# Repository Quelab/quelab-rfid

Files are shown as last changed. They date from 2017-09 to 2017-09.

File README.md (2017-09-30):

# Arduino Code for Quelab RFID reader
This project is intended to replace the code that was originally running on the RFID door control system for Quelab.

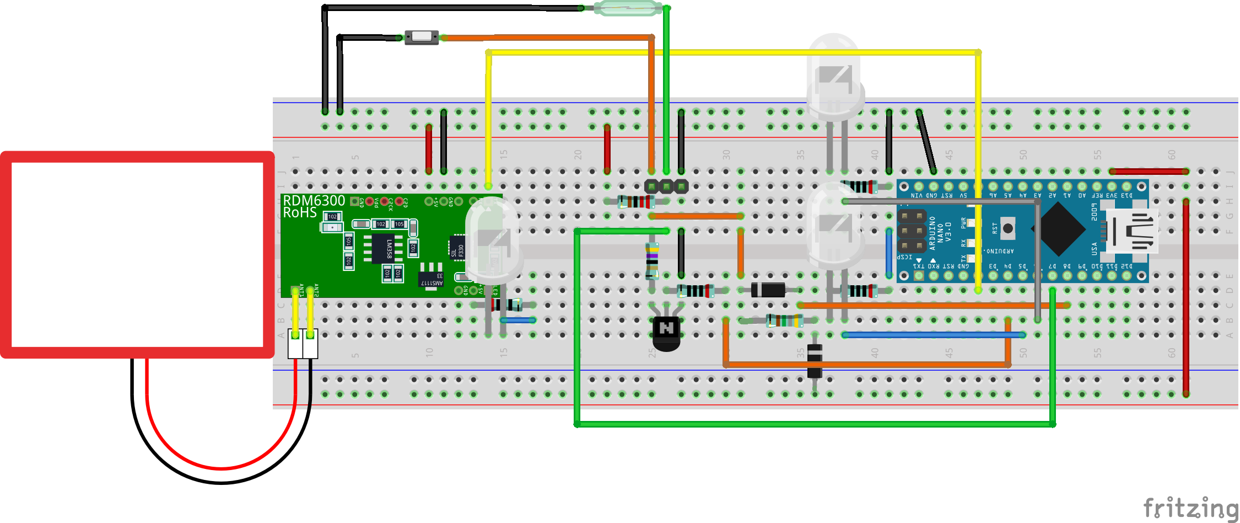
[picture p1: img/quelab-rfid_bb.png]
circuit


The program just runs in a loop doing the following:
* Listen for input from the USB serial port connected to a PC
* Read events from RFID reader
* Process sensor Input from Door Lock, Door Open
* Handle periodic Timer events to either relock the door, or send Status of Health

Previously there was hardware connected to control an Open Sign, but this will most likely not be used in the current implementation to simply wiring connections.

## Build/Deploy
The most automated way to build/deploy to an arduino nano is using docker. The easiest is likely with Arduino UI.

## Docker under Linux
Just connect the arduino devices USB (assuming /dev/ttyUSB0) port to your computer and issue the following
commands:

```bash
docker build -t quelab-rfid-arduino .
docker run -it --rm --device=/dev/ttyUSB0 -v $(pwd):/sketch quelab-rfid-arduino upload
```

Other Commands available:
* bash
* build
* monitor (uses gnu screen exit with 'Ctrl-a \')
* upload

# Implementation Details
## Hardware

* [Schlage Electronic Lock](https://www.amazon.com/dp/B001GPL5WU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)
* [Arduino Nano](https://store.arduino.cc/usa/arduino-nano)
* [RDM6300](https://www.itead.cc/wiki/RDM6300)
    - clock drift is pretty severe on the device I bought. I have to restart the device once a day to be able to effectively read cards again.

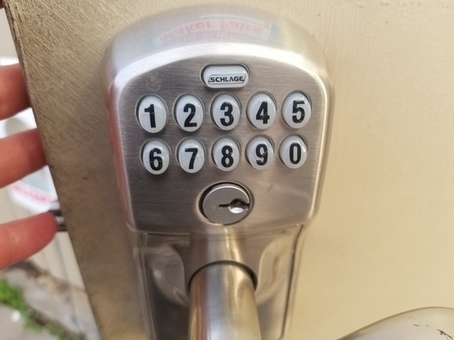
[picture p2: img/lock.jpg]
lock
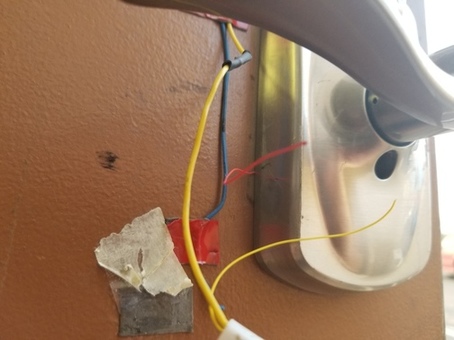
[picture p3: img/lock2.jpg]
lock2
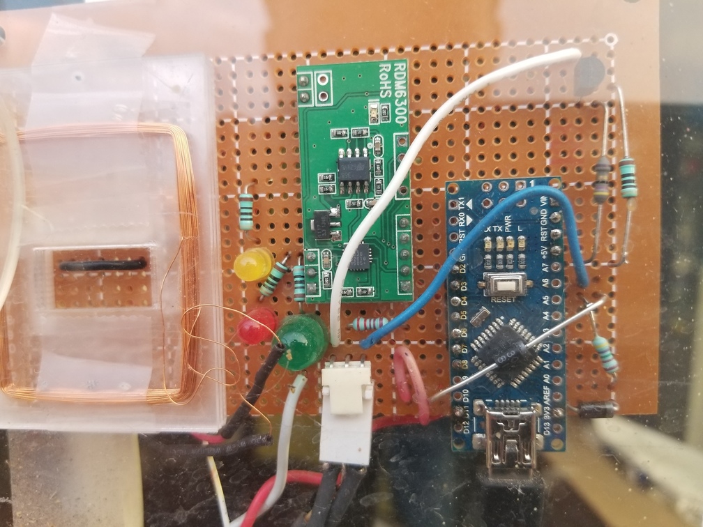
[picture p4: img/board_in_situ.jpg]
board
  

## Protocol Data Link Layer
The data link layer uses a simplified ISO [High-level Data Link Control](https://en.wikipedia.org/wiki/High-Level_Data_Link_Control).

| Flag  | Information | FCS | Flag |
|---|---|---|---|
|8 bits | Variable length, n * 8 bits | 16 bits |8 bits|
| ~ | [payload] |[xmodem crc16]| ~ |

All serial communication is processed a single byte at a time. This allows the Arduino to do other processing without getting bogged down handing serial communications. It uses a pretty standard Frame start/end flag 0x7e *~*. The HDLC used here is somewhat non standard because it lacks some features like address (unnecessary for peer communications) and Control.

The HDLC implementation is taken from a library found online and modified to use xmodem crc in place of the PPP CRC16. This is mostly because xmodem CRC seems to be better supported.

* [HDLC library](https://github.com/jarkko-hautakorpi/Arduhdlc) &rarr; [modified HDLC library](https://github.com/kak-bo-che/Arduhdlc) (my fork to use xmodem crc instead of PPP)
* [CRC FAQ](http://www.ross.net/crc/download/crc_v3.txt)

## Protocol Application Layer
The application layer protocol is simply [JSON](www.json.org). JSON is probably an unexpected choice for arduino communications because it is super verbose and would be a waste of memory for complicated applications. I attempted to use Google's [MessagePack](http://msgpack.org/index.html) initially, but couldn't find a library that played nicely with the HLDC used for communications. One advantage of JSON though is it is widely supported in all programming languages w/o add on libraries and it is human readable. In the future it may be necessary to increase the [ArduinoJSON buffer](https://bblanchon.github.io/ArduinoJson/assistant/) if larger messages are necessary.
JSON makes it easy to write a PC application that communicate with the Arduino.

### Example Communications:

#### Status of Health Message (Arduino &rarr; PC)
```json
{"message":"status","door_open":true,"locked":true,"lock_open":false}
```
#### RFID Read Message (Arduino &rarr; PC)
```json
{"message":"rfid_card","rfid_hex":"62E3086CED08","rfid":552173}
```

#### Unlock Door (PC &rarr; arduino)
```json
{"message": "lock_ctrl", "unlock": true}
```

## Arduino Libraries Used
* [RDMS630 library](https://github.com/electronicdrops/RFIDRdm630/) Used to communicate with the RFID reader over a bit bang serial port
* [ArduinoJson](https://github.com/bblanchon/ArduinoJson.git) Building and Parsing JSON data, could be done manually but there is no kill like overkill...
* [elapsedMillis](https://github.com/pfeerick/elapsedMillis.git) Makes access to built in timer of the Atmel chip simple.

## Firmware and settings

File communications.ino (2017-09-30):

#include <SoftwareSerial.h>
#include "RFIDRdm630.h"
#include "Arduhdlc.h"
#include <ArduinoJson.h>
#include <elapsedMillis.h>

typedef enum {
  closed = 0,
  open = 1
} switch_state_t;

typedef enum {
  unlocked = 0,
  locked = 1
} lock_state_t;

typedef enum {
  no_action = 0,
  lock_door = 1,
  unlock_door = 2
} action_flags_t;

typedef struct switch_status {
    uint32_t last_change_time;
    uint8_t input_pin;
    union {
        switch_state_t debounced_door_state;
        lock_state_t debounced_lock_state;
    };
    union {
        switch_state_t last_door_state;
        lock_state_t last_lock_state;
    };
} switch_status_t;

#define BOUNCE_PERIOD 200 //Contact switch state changes less than this period are considered bounces

/* Pre-allocated buffers
1) ArduinoJson Buffer > raw message buffer see online calculator
2) HDLC message buffer > slightly larger than raw buffer
3) raw message buffer > actual json bytes
*/
// messages sent over serial and the maximum size of a message in bytes
const size_t CRC_SIZE = 2;
const size_t FRAME_CHARS = 2;
const size_t max_message_size = 124;

// 1 bytes for constructing JSON data
StaticJsonBuffer<200> jsonBuffer;

// 2 buffer allocated for HDLC communications
const size_t max_hdlc_frame_length = max_message_size + CRC_SIZE + FRAME_CHARS;

// 3 raw message buffer
char send_message_buffer[max_message_size];
size_t send_message_size = 0;

// IO pins
const unsigned int rxPin = 2;  // pin that will receive the data
const unsigned int txPin = 3;  // connection not necessary.
const unsigned int lock_ctrl = 4; // Set high to signal door to unlock
const unsigned int red_led = 5;   // Turn on to indicate  locked key
const unsigned int green_led = 6; // Turn on to indicate unlocked key
const unsigned int door_contact = 7; // Is low when contact switch indicates door is closed
const unsigned int lock_contact = 8; // Is low when electronic lock indicates door is unlocked

switch_status_t door_status;
switch_status_t lock_status;
int i = 0;

// RFID
RFIDtag  tag;  // RFIDtag object
RFIDRdm630 reader = RFIDRdm630(rxPin,txPin);

// Timer
elapsedMillis lock_timer;
elapsedMillis status_of_health_timer;
const unsigned int unlocked_interval = 5000; /* Lock is open for 5 seconds */
const unsigned int status_of_health_interval = 30000; /* health status every 30s */

boolean lock_timer_active;
action_flags_t action_flag = no_action;

/* Function to send out byte/char */
void send_character(uint8_t data);

/* Function to handle a valid HDLC frame */
void hdlc_frame_handler(const uint8_t *data, uint16_t length);

/* Initialize Arduhdlc library with three parameters.
1. Character send function, to send out HDLC frame one byte at a time.
2. HDLC frame handler function for received frame.
3. Length of the longest frame used, to allocate buffer in memory */
Arduhdlc hdlc(&send_character, &hdlc_frame_handler, max_hdlc_frame_length);

/* Function to send out one 8bit character */
void send_character(uint8_t data) {
    Serial.print((char)data);
}

void lockDoor(){
    lock_timer_active = false;
    digitalWrite(lock_ctrl, LOW);
}

void unlockDoor(){
    lock_timer = 0;
    lock_timer_active = true;
    digitalWrite(lock_ctrl, HIGH);
}

/* Frame handler function. What to do with received data? */
void hdlc_frame_handler(const uint8_t *data, uint16_t length) {
    // Do something with data that is in framebuffer
    JsonObject& root = jsonBuffer.parseObject(data);
    if (root.success()) {
        String command = root["message"];
        if (command == "lock_ctrl"){
            bool unlock = root["unlock"];
            if (unlock == true){
                action_flag = unlock_door;
            } else {
                action_flag = lock_door;
            }
        }
    }
    jsonBuffer.clear(); // global buffer is not reused otherwise
}

void sendStatus(){
    JsonObject& root = jsonBuffer.createObject();
    root["message"] = "status";
    root["door_open"] = (door_status.debounced_door_state == open)? true: false;
    root["locked"] = (lock_status.debounced_lock_state == locked)? true: false;
    root["lock_open"] = (digitalRead(lock_ctrl)? true: false);
    send_message_size = root.printTo(send_message_buffer, max_message_size);
    hdlc.frameDecode(send_message_buffer, send_message_size);
    jsonBuffer.clear(); // global buffer is not reused otherwise
}

void sendTagInfo(RFIDtag  *tag){
    JsonObject& root = jsonBuffer.createObject();
    root["message"] = "rfid_card";
    root["rfid_hex"] = tag->getTag();
    root["rfid"] = tag->getCardNumber();
    send_message_size = root.printTo(send_message_buffer, max_message_size);
    hdlc.frameDecode(send_message_buffer, send_message_size);
    jsonBuffer.clear(); // global buffer is not reused otherwise
}

char switchState(switch_status_t *switch_status) {

  unsigned long newtime;
  switch_state_t current_state;

  current_state = (switch_state_t) digitalRead(switch_status->input_pin);
  newtime=millis();

  if(current_state != switch_status->last_door_state) {
    switch_status->last_door_state = current_state;
    switch_status->last_change_time=newtime;
  } else if((newtime - switch_status->last_change_time) >= BOUNCE_PERIOD){
    switch_status->debounced_door_state = current_state;
  }
  return switch_status->debounced_door_state;
}

void processSwitches() {
  /* Send a message based on Door State + Door Lock State */
  static switch_state_t last_door_state = closed;
  static lock_state_t last_lock_state = locked;

  switchState(&door_status);
  switchState(&lock_status);

  if (door_status.debounced_door_state != last_door_state ||
      lock_status.debounced_lock_state != last_lock_state){
    last_lock_state = lock_status.debounced_lock_state;
    last_door_state = door_status.debounced_door_state;
    digitalWrite(red_led,  lock_status.debounced_lock_state);
    digitalWrite(green_led, !lock_status.debounced_lock_state);

    sendStatus();
  }
}

void setup() {
    pinMode(1,OUTPUT); // Serial port TX to output
    pinMode(lock_ctrl, OUTPUT);
    pinMode(red_led, OUTPUT);
    pinMode(green_led, OUTPUT);
    pinMode(door_contact, INPUT);
    pinMode(lock_contact, INPUT);

    door_status.input_pin = door_contact;
    door_status.last_door_state = open;
    door_status.debounced_door_state = open;
    door_status.last_change_time = 0;

    lock_status.input_pin = lock_contact;
    lock_status.last_lock_state = locked;
    lock_status.debounced_lock_state = locked;
    lock_status.last_change_time = 0;

    digitalWrite(green_led, lock_status.debounced_lock_state);
    digitalWrite(red_led, !lock_status.debounced_lock_state);
    digitalWrite(lock_ctrl, LOW);

    lock_timer_active = false;

    // initialize serial port to 9600 baud
    Serial.begin(9600);
}

void loop() {
    processSwitches();

    if (reader.isAvailable()){  // tests if a card was read by the module
        tag = reader.getTag();  // if true, then receives a tag object
        sendTagInfo(&tag);
    }
    if (status_of_health_timer >= status_of_health_interval){
        status_of_health_timer -= status_of_health_interval;
        sendStatus();
    }
    if (lock_timer_active && lock_timer >= unlocked_interval){
        lockDoor();
        sendStatus();
    }
    if (action_flag == lock_door){
        lockDoor();
        sendStatus();
        action_flag = no_action;
    }
    if (action_flag == unlock_door){
        unlockDoor();
        sendStatus();
        action_flag = no_action;
    }
}

/*
SerialEvent occurs whenever a new data comes in the
hardware serial RX.  This routine is run between each
time loop() runs, so using delay inside loop can delay
response.  Multiple bytes of data may be available.
*/
void serialEvent() {
    while (Serial.available()) {
        // get the new byte:
        char inChar = (char)Serial.read();
        // Pass all incoming data to hdlc char receiver
        hdlc.charReceiver(inChar);
    }
}

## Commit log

2017-09-25 remove opensign relay controls
2017-09-25 adding fritzing breadboard layout
    [quelab-rfid.fzz]
